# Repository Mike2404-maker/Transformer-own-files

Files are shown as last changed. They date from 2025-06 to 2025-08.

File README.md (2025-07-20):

# Transformer-own-files
Here i share my own files of this Transformer Build 
this files i use in my transformer of Michael rechtin, this repository include bom list, pinmapping, gerber file for my own PCB, everything is free to share

Sideplates you have to do in Carbon plate 1.5mm or 2mm depends on you. i try in pla but its much to heavy

the file called stabrolle is a 3mm pin you can use as bearing for the 4 wheels if i remember right you need 15 or 16 pieces for one bearing. so you can print 60 pieces to get all for the wheel bearing, saves wheight otherwise you can use steel rods. 

my boom will be updatet with the screws in future
the pinmapping you can also use at nicholas rehm drehmflight vtol at github. 

the gerber file you can use over JLC PCB to get your own pcb to wire all of this transformer. ( but its in a testing period.) check file before you order. Everything you do with this files on this repository is at your own risk.

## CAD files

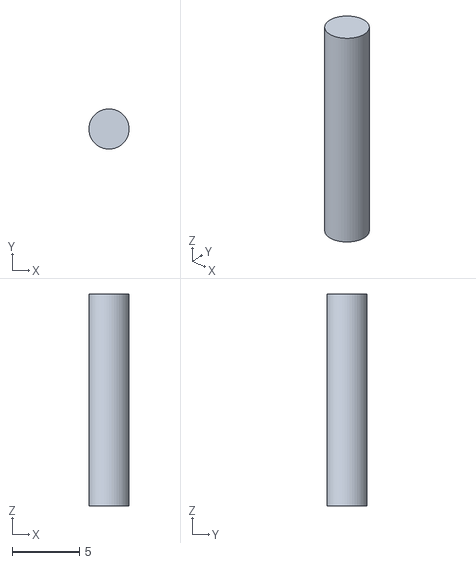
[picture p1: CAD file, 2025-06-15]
stabrolle transformer.stl
3.00 x 3.00 x 15.8

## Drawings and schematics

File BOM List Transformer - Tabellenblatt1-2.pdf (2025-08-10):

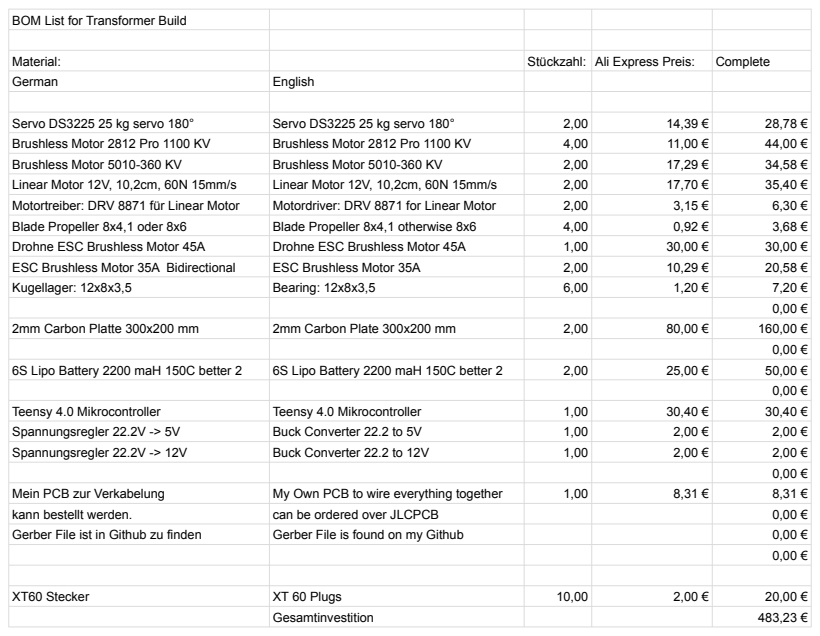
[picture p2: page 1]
Material:; Stückzahl: Ali Express Preis:; Complete; German; English; Servo DS3225 25 kg servo 180°; Brushless Motor 2812 Pro 1100 KV; Brushless Motor 5010-360 KV; Linear Motor 12V, 10,2cm, 60N 15mm/s; Motortreiber: DRV 8871 für Linear Motor; Motordriver: DRV 8871 for Linear Motor; Blade Propeller 8x4,1 oder 8x6; Blade Propeller 8x4,1 otherwise 8x6; Drohne ESC Brushless Motor 45A; ESC Brushless Motor 35A Bidirectional; ESC Brushless Motor 35A; Kugellager: 12x8x3,5; Bearing: 12x8x3,5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

BOM List for Transformer Build

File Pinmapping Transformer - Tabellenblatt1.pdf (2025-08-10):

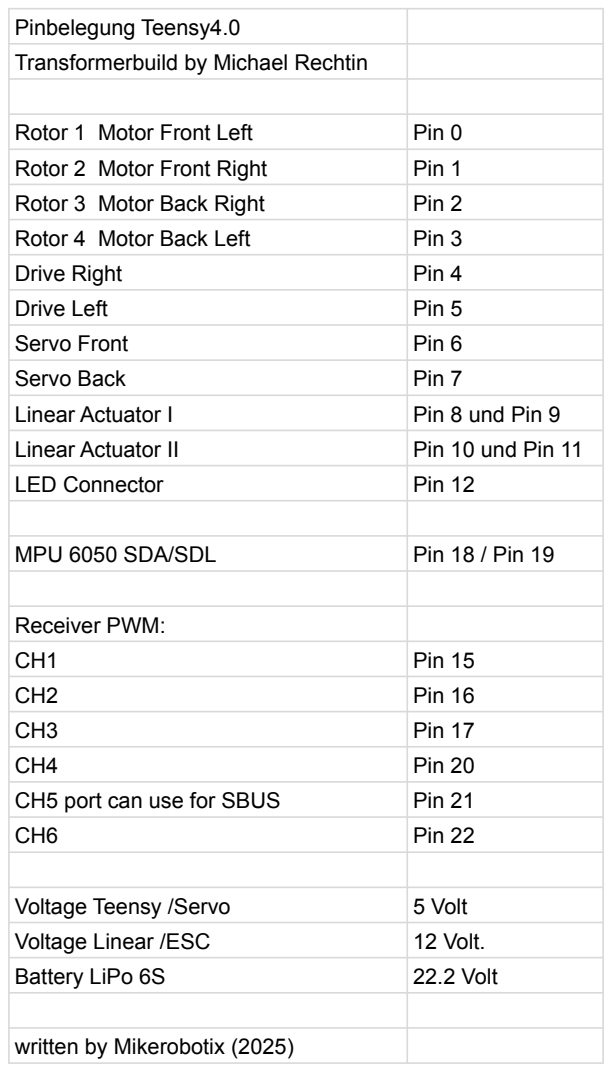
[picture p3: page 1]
Rotor 1 Motor Front Left; Pin 0; Rotor 2 Motor Front Right; Pin 1; Rotor 3 Motor Back Right; Pin 2; Rotor 4 Motor Back Left; Pin 3; Drive Right; Pin 4; Drive Left; Pin 5; Servo Front; Pin 6; Servo Back; Pin 7; Linear Actuator I; Pin 8 und Pin 9; Linear Actuator II; Pin 10 und Pin 11; LED Connector; Pin 12; MPU 6050 SDA/SDL; Pin 18 / Pin 19; Receiver PWM:; Pin 15; Pin 16; Pin 17; Pin 20; CH5 port can use for SBUS; Pin 21; Pin 22; Voltage Teensy /Servo; 5 Volt; Voltage Linear /ESC; 12 Volt.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

Pinbelegung Teensy4.0
Transformerbuild by Michael Rechtin

written by Mikerobotix (2025)
